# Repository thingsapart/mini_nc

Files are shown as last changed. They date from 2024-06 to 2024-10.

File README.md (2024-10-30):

# MiniNC
The V0 of CNC machines - small envelope with 200x150x70mm (8x6x2.75") work area, aims to cut alu well (enough).

# Discussion
There's a [small discord](https://discord.gg/6VSBqa9H) discussing this machine (and other) small CNCs.

# MiniNC - What is it?
A true small _Desktop CNC_ machine that can be used inside an apartment in a pinch but can still cut softer metals. One that does not require a full shop due to space, mess and noise and does not break the bank. [Current BOM cost is around $500](https://github.com/thingsapart/mini_nc/blob/main/docs/MiniNC%20BOM%20-%20BOM.tsv) with most parts ordered on Amazon, excluding the price to cut the plywood panels (that can add another $100-200 if not diy'd). We're still working on the noise part currently.

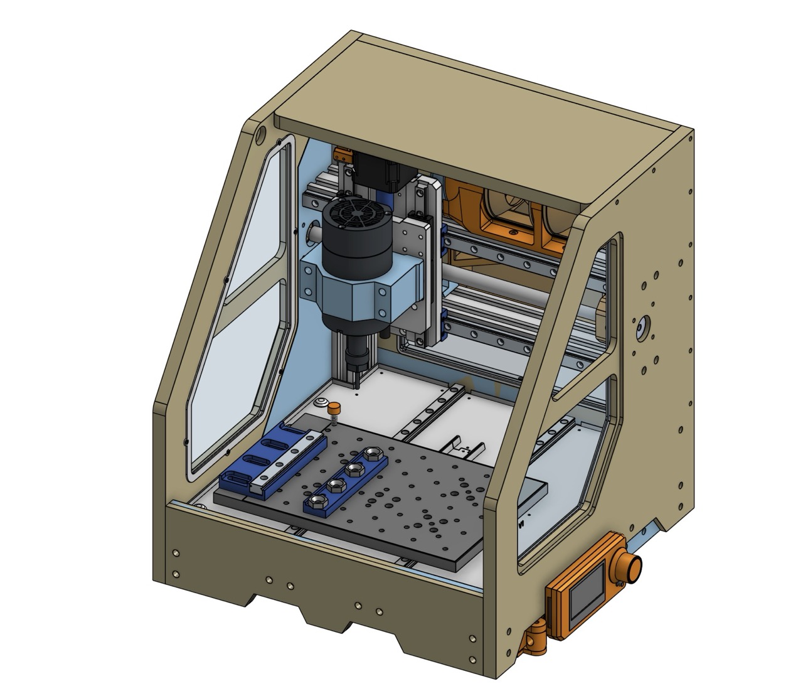
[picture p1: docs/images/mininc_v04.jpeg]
Current status with 300W BLDC spindle, vise, chipvac V2, 3d-touch-probe support, ...


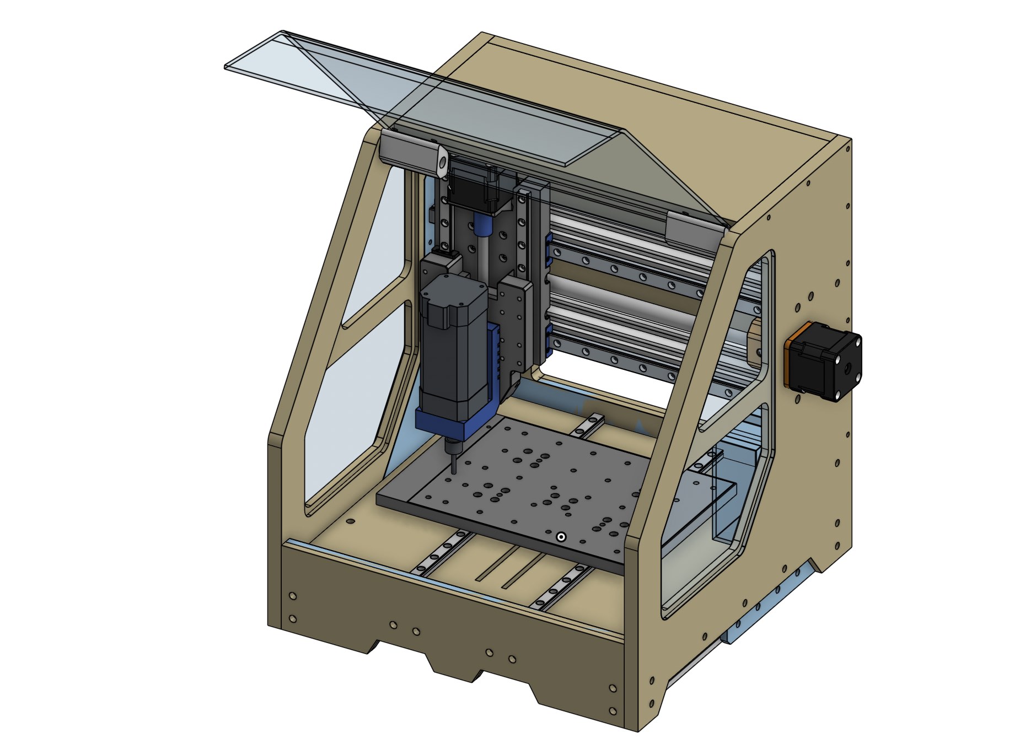
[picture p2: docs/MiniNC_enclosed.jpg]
MiniNC enclosed


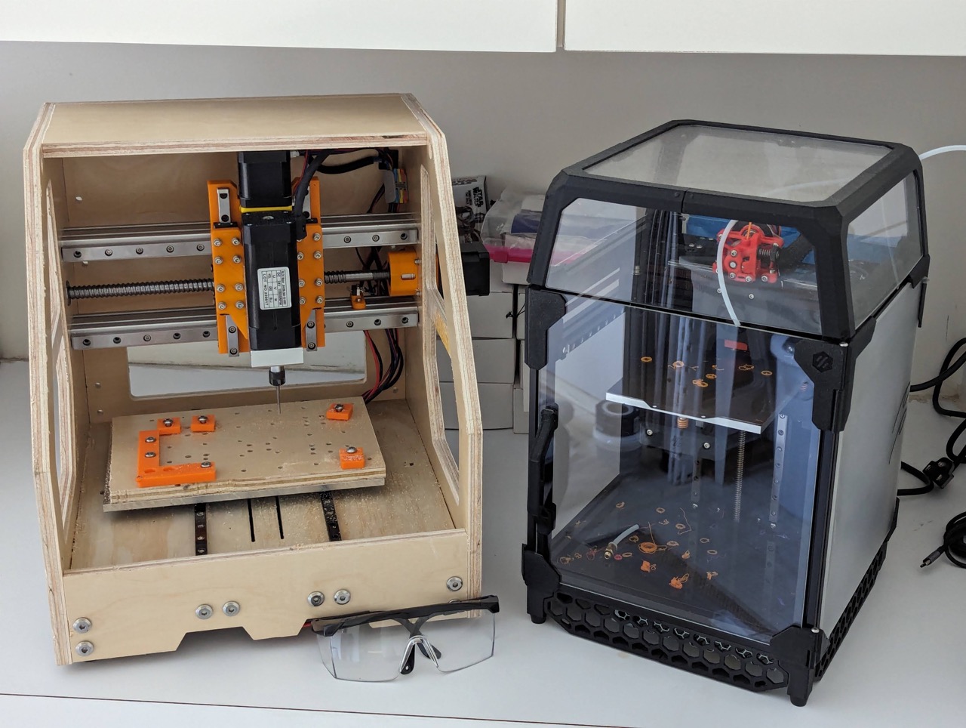
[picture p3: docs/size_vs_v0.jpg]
Size compare to Voron V0.1


## ⚠️ WARNINGS ⚠️
### Danger
CNC machines are a lot more dangerous than 3D printers. BUILD AT YOUR OWN RISK. DO NOT OPERATE "OPEN" OR WITHOUT POLYCARBONATE WINDOWS. TURN OFF THE MACHINE WHEN CHANGING END MILLS OR CHANGING WORK PIECES - DO NOT LEAVE IT POWERED ON WHILE HANDS ARE INSIDE THE ENCLOSURE.
### Alpha
The machine is past the main design phase and a prototype has been built and is about to get tested. But that does not mean everything is finalized.

## Some Results

35x15mm test cut on the first prototype machine (untrammed, excuse the bottom finish) - with 3D-printed ABS X- and Z-plates:
<table style="border: 1px white; border-collapse: collapse;">
  <tr>
    <td rowspan=2>
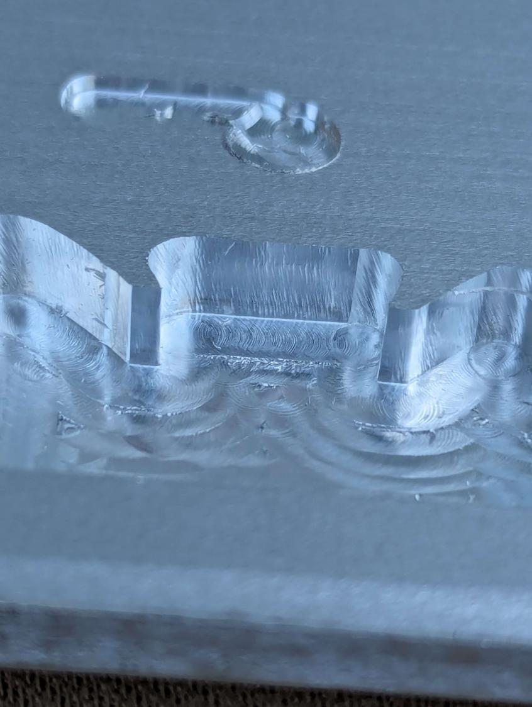
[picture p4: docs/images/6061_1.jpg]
      
    </td>
    <td>
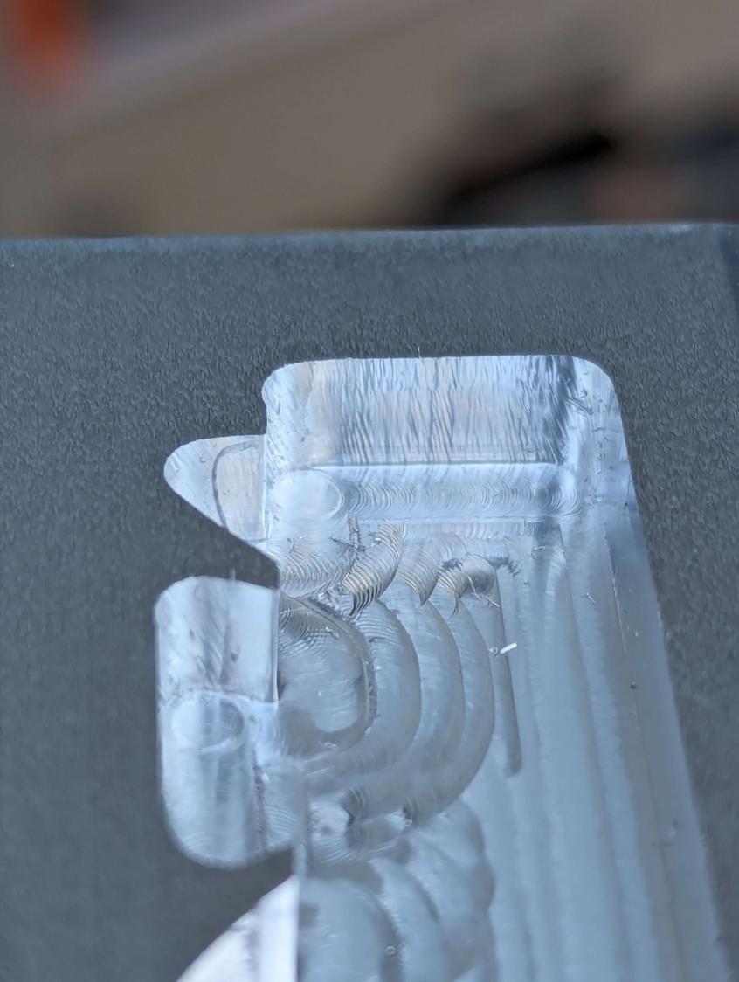
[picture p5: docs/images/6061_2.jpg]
      
    </td>
  </tr>
  <tr>
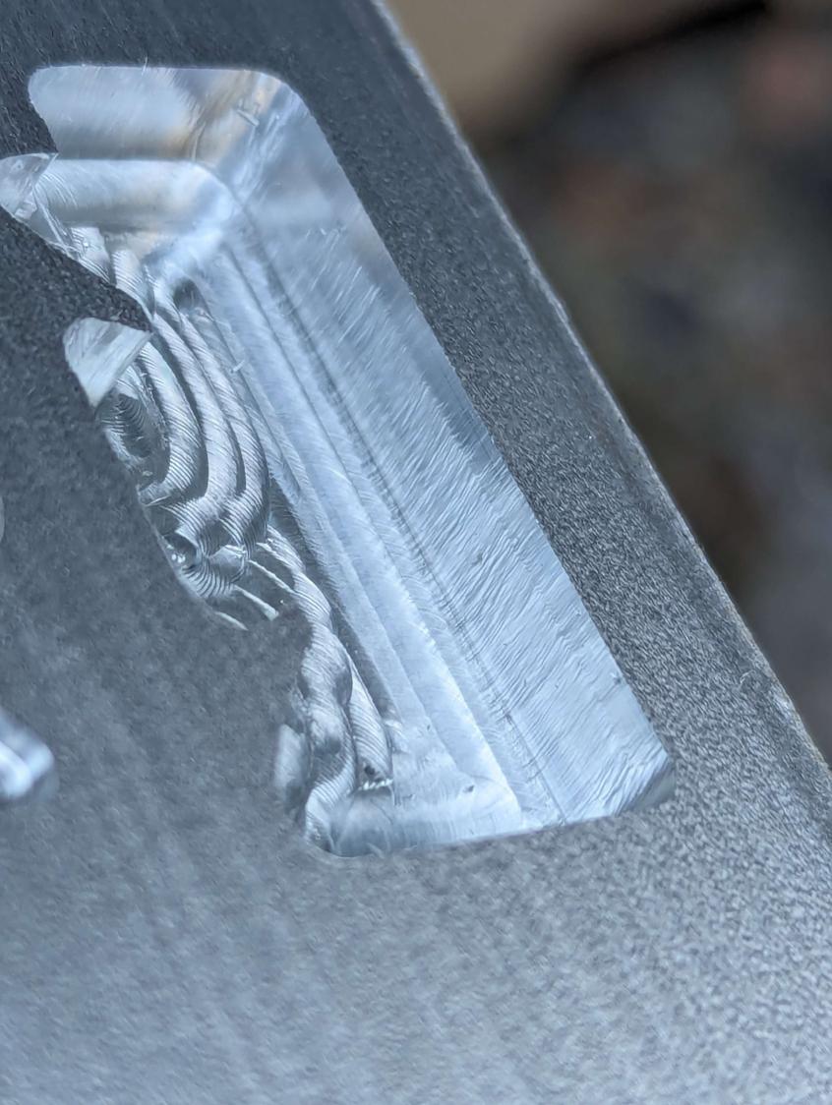
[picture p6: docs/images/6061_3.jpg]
    <td></td>
  </tr>
</table>

## Requirements
* Cuts aluminium well.
* Cost-efficient.
* Space-efficient.
* As quiet as possible.
* Not too messy.

## Inspiration/Credits
This design was influenced by the [Milk Cr8](https://www.milkcr8cnc.com) ([GH](https://github.com/Makers-On-Tap/milkcr8-cnc)) CNC's use of plywood as a stiff box structure to enclose and stiffen the machine at the same time. The idea was to use the wooden structure and combine it with aluminium extrusions to simplify the build while retaining some of the improved dampening over just an alu extrusion structure.

## Features
* Cuts aluminium well =>
   * Rigid (enough) => smaller size, slower feeds, single flute, smaller end mills,
   * As it won’t be the stiffest machine, make it well-dampened => not fully made of alu, use steel, epoxy granite and wood to dampen some of the vibrations,
   * Smaller, low-powered spindles 100-500W,
   * chip-evacuation system => CPAP or chip fan,
   * cooling via misting and air blast.
* Cost-efficient =>
   * Standard components => MGN12/MGN9 rails, small 100-500W spindles, 20 series extrusions for some of the structure,
   * smaller, lower-cost spindles,
   * smaller size.
* Space-efficient =>
   * gantry design => high space-efficiency, can be reasonably rigid in this smaller envelope
   * Smaller size to cut smaller parts fitting target use-cases,
* Beginner-Friendly =>
   * XYZ probe + tool setter + surface meshing,
   * community presets and forums,
   * custom interface for Duet RRF (much later),
      * source  + G-Code + Instructions packages like Coast Runner
      * Integrated forums,
      * g-code visualizer and simulated pre-runner including stock dimensions.
* As quiet as possible =>
   * fully enclosed and ideally tightly sealed,
   * interior/exterior sound insulation (?) => layer of foam + outer layer of ACM panels?,
   * no compressor,
   * BLDC spindles with reduced vibrations.
* Not too messy =>
   * fully enclosed (!),
   * dust extraction => CPAP or roborock fan,
   * misting but no flood cooling.

## Who is it for?
* Makers and 3D printer enthusiasts but really anyone without a full (metal-working) shop and/or space for a larger machine.
* Anyone without the space for one of the larger machines.

## Stiffness

The current wooden frame seems decently stiff at roughly 1N/&micro;m in Y at the spindle collet even with 3D printed X/Y plates - needs more testing though but seems like a good start.

Some general numbers I've found for comparison:
* [Siecni 12x30 Longmill MK2 ~ 0.07N/&micro;m X and 0.05N/&micro;m Y](https://sienci.com/wp-content/uploads/2022/09/Stiffness-Rating-with-Commentary.pdf),
* [MPCNC ~ 0.1-0.2N/&micro;m](https://forum.v1e.com/t/deflection-measurement/37968/34),
* [burly but _large_ CNC build ~ 1-3N/&micro;m](https://www.mycncuk.com/threads/7155-stiffness-measurements-cnc-mk3),
* I've seen 20N/&micro;m recommended for cutting alu very well,
* Milling Machines supposedly ~ 20-30N/&micro;m,
* professional cast-iron or epoxy granite VMCs are on the other 70-150N/&micro;m.
* (LET ME KNOW IF YOU HAVE OTHER/MORE DATA OR CORRECTIONS, I'D LOVE TO ADD IT)
  
NB: [Load cell tool design to apply a measured/specific force to the spindle](https://www.printables.com/model/473947-xy-forcing-mechanism-for-cnc-router-diagnostics).
NB: [Some numbers and suggested values for stiffness](https://www.cnczone.com/forums/uncategorised-metalworking-machines/378098-cnc-2.html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) - 25kgf ~> <0.1mm deflection seems like a decent goal (2.5N/&micro;m).

Rough design for phase-2 buildout using a lasercut steel structure to increase stiffness if needed. 
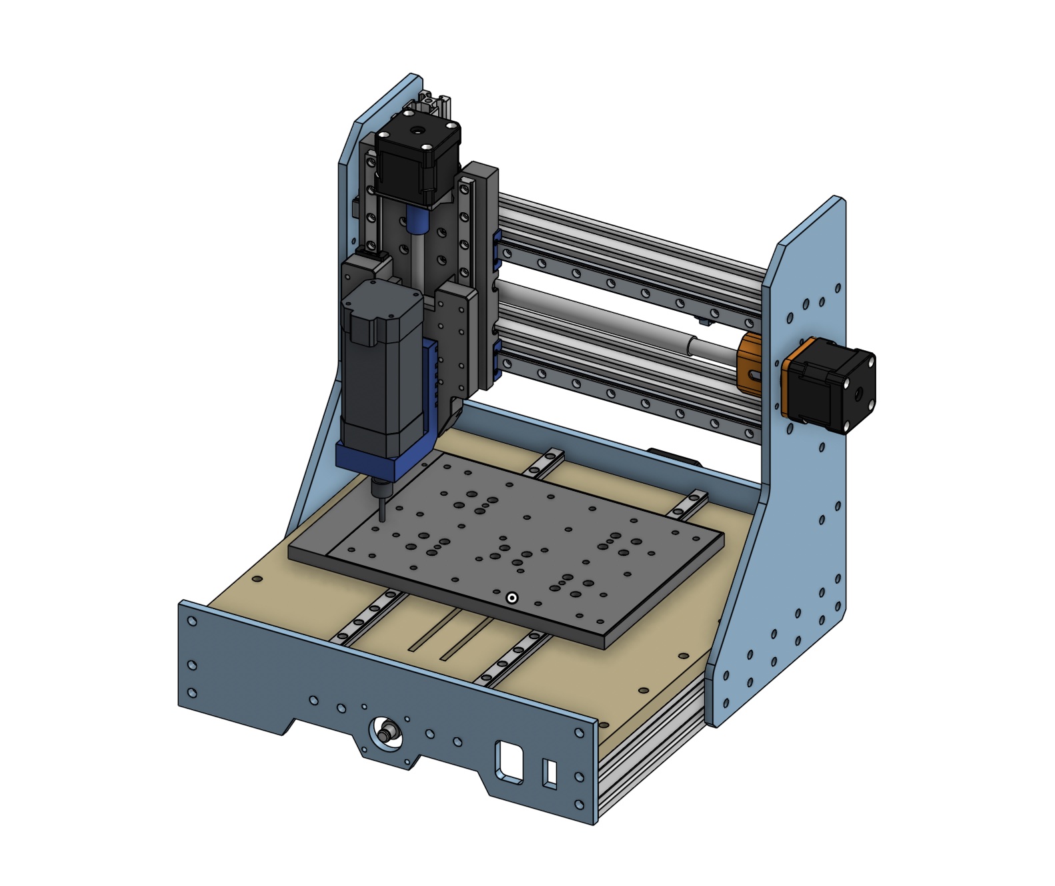
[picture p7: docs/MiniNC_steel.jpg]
Steel structure under enclosure panels


## Chip Vac / Dust Extraction

Finished a small prototype chip-vacuum based on a Roborock/Xiaomi/MiJia vacuum fan and [Roborock-CPAP PCB](https://github.com/condottab/Roborock-CPAP). Additional cost is only ~$15 for the 2kPa fan versions or ~$30 for the (untested) 4-5kPa version.

V2 of the chip vac in a tubular form has been designed and tested, seems to work a tad better than V1 and less prone to clogging, easier to clean.

Supports different "duct attachments" held in place via magnets, which makes it easy to
* remove when changing end mills or cleaning parts of the machine,
* changing the type of attachment (there's currently an open and a closed version with a "curtain", one for better suction, one for better visibility).

Current V2:

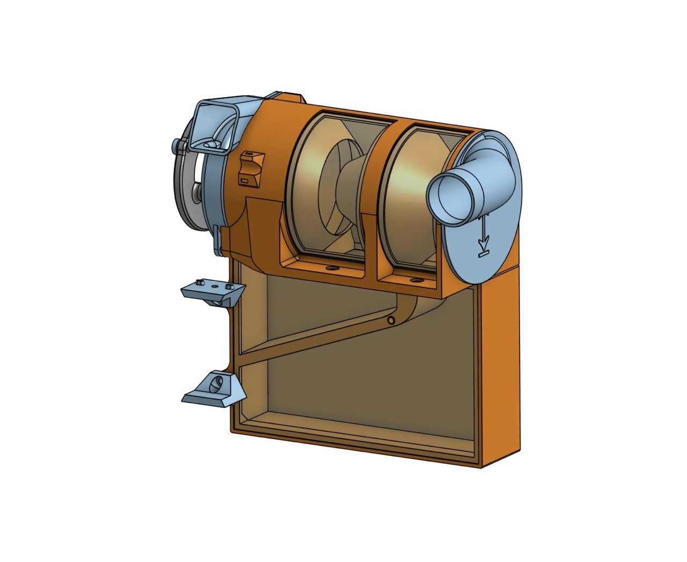
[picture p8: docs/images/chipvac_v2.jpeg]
Chipvac V2


Original V1:

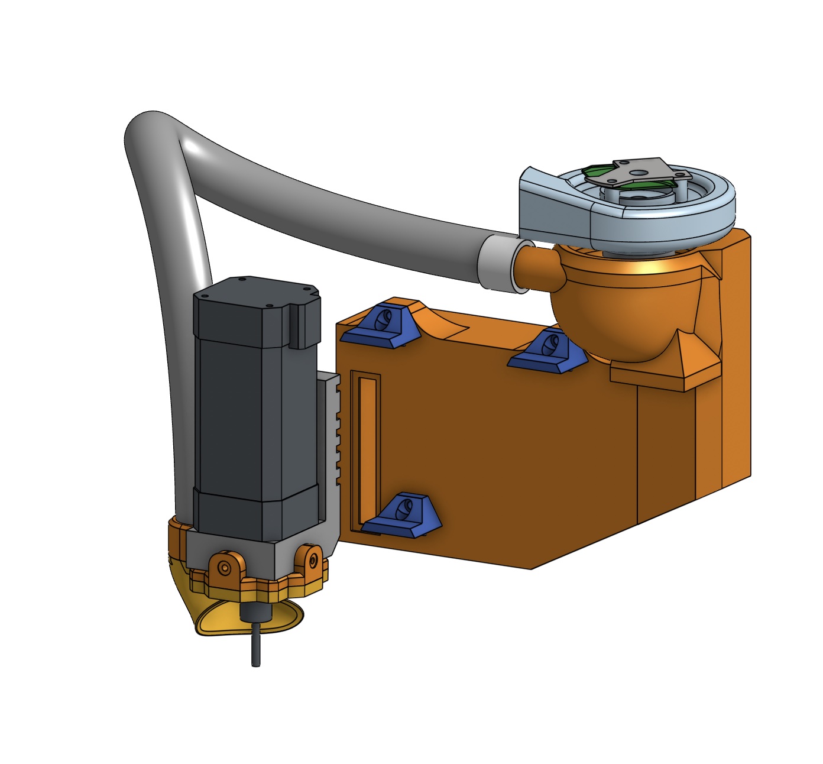
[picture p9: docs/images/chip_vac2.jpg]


## Use-Cases
* Small aluminium parts:
   * high-speed 3D printer motion system reinforcements and brackets,
   * higher-temp 3D printer component,
   * toolhead components.
* Makers:
   * Tools, …

## Optional Features/TODOs
* 🏗 low-profile modular vise system (untested design in V0.2),
* internal camera,
* laser Module Support,
* 🏗 internal LED lighting + toolhead lighting (basic design with room for improvement in V0.2),
* 4th axis?

## Releases
* V0.1 - Initial Release.
* V0.2 - 07/2024
  * Many, many minor improvements after alpha-testing prototype,
  * roboroc-based chip-vac,
  * interla left/right side LEDs,
  * electronics mounts,
  * support for 300W BLDC spindle (36-48V),
  * prototype of MGN9-jaw-based low profile vise,
  * prototype toolsetter (through-bed with fixed switch mounted to bottom panel.
 
[Onshape Document](https://cad.onshape.com/documents/c86121a300cc3efe8d19b16b/w/b3c26184b681d889100ca699/e/cecf7ca72a42132848999341)

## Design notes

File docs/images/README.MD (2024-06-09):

Image files of the machine and samples made with it.

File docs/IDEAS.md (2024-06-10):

# Some (crazy) ideas

## CPAP/Roborock Push-Pull dust extraction and chip blower

Cyclone dust/chip extractor based on a CPAP or Robrock vacuum/blower. Hook up the input port for extraction, the output port for chip blowing and/or misting.

Half of the dust shoe is detachable and held via magnets, the alterantive would be to have two "dust shoe attachments" - one for blowing config, the other for vacuuming.

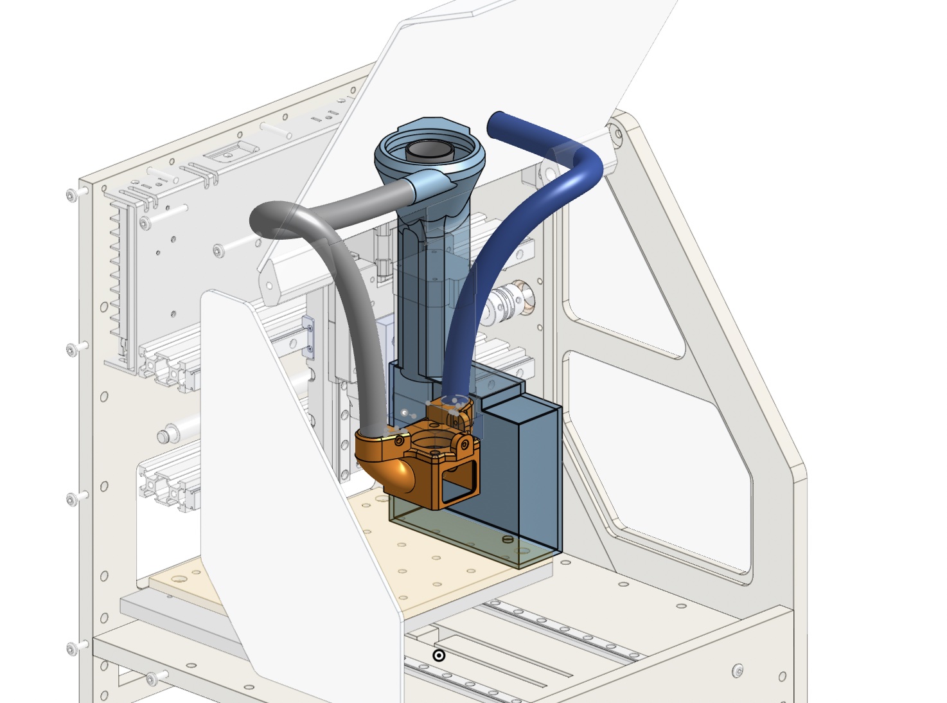
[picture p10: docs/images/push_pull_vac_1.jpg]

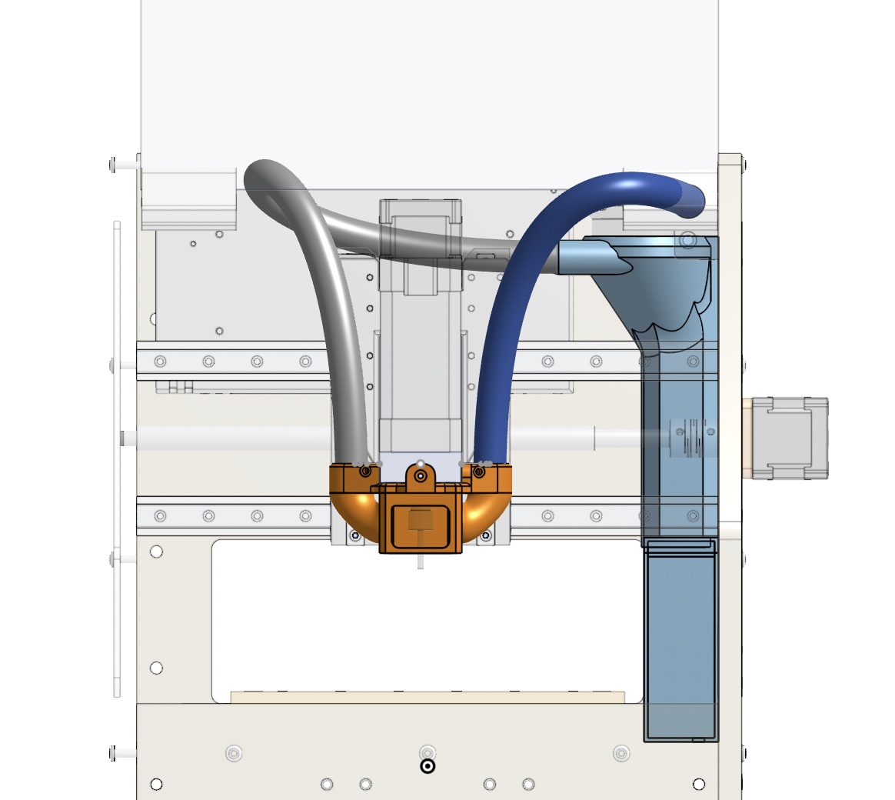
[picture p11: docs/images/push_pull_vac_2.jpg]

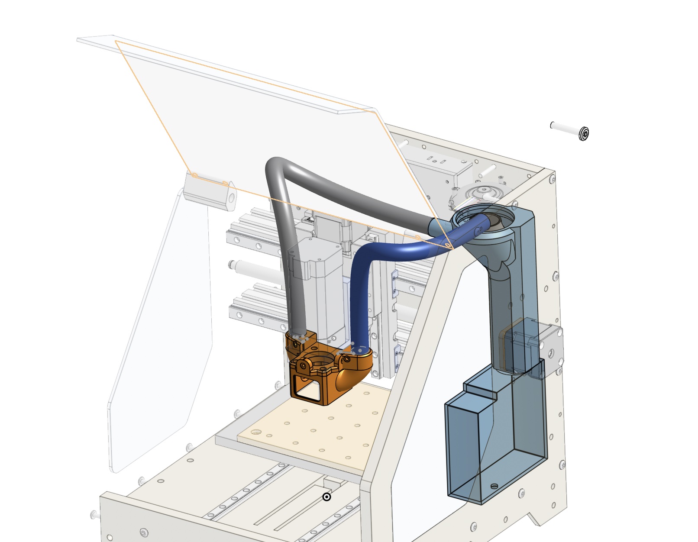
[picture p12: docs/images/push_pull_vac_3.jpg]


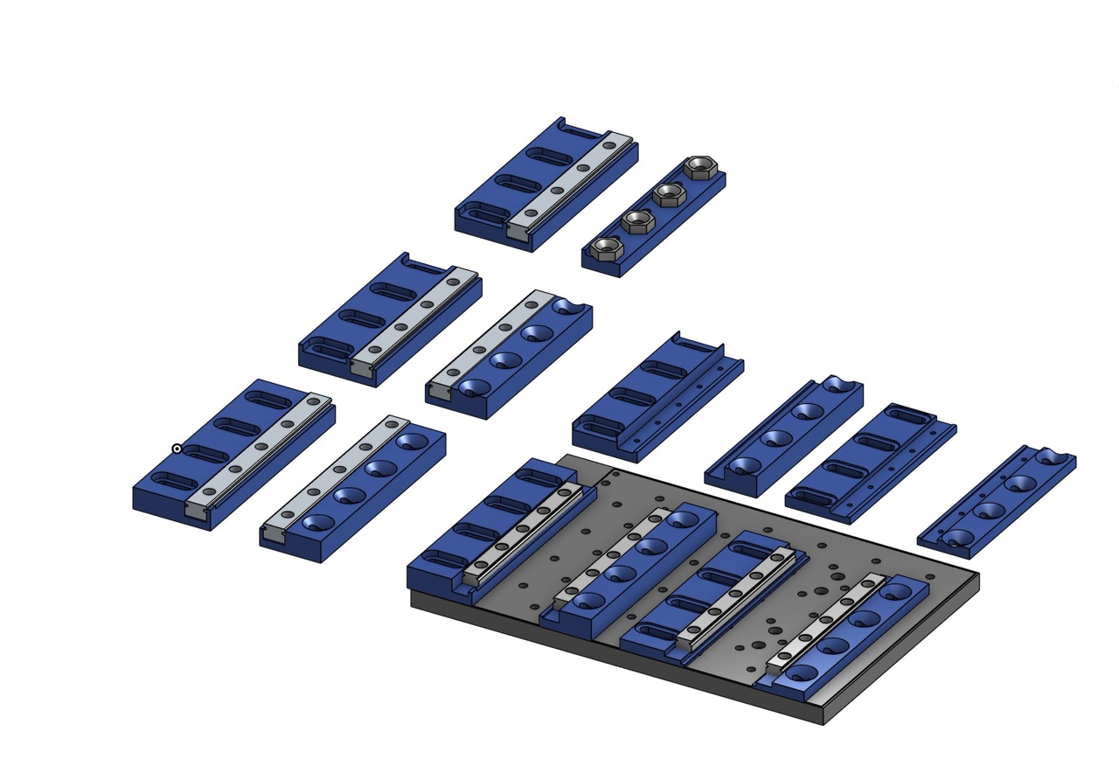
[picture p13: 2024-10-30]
docs/images/vises_v2.jpeg

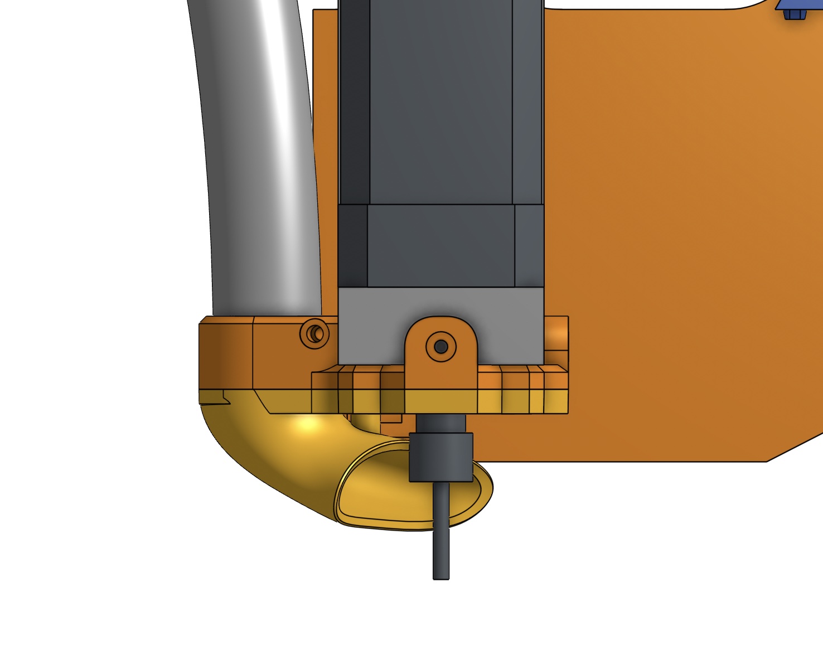
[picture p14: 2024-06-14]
docs/images/chip_vac_open.jpg

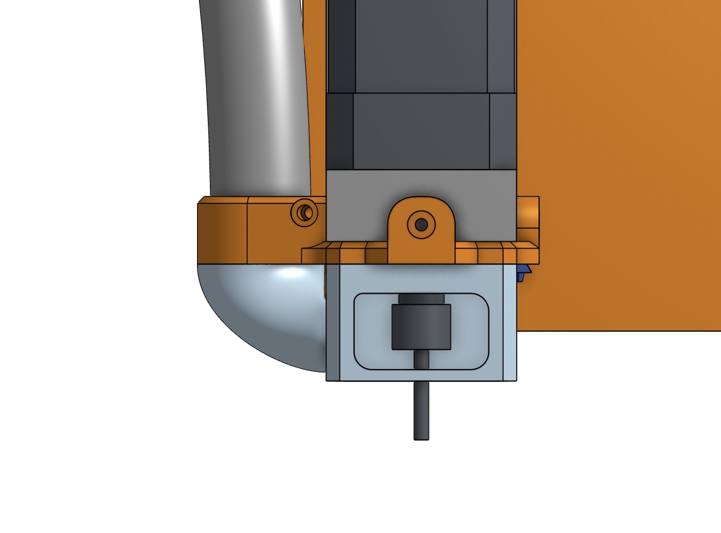
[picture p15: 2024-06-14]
docs/images/chip_vac_closed.jpg

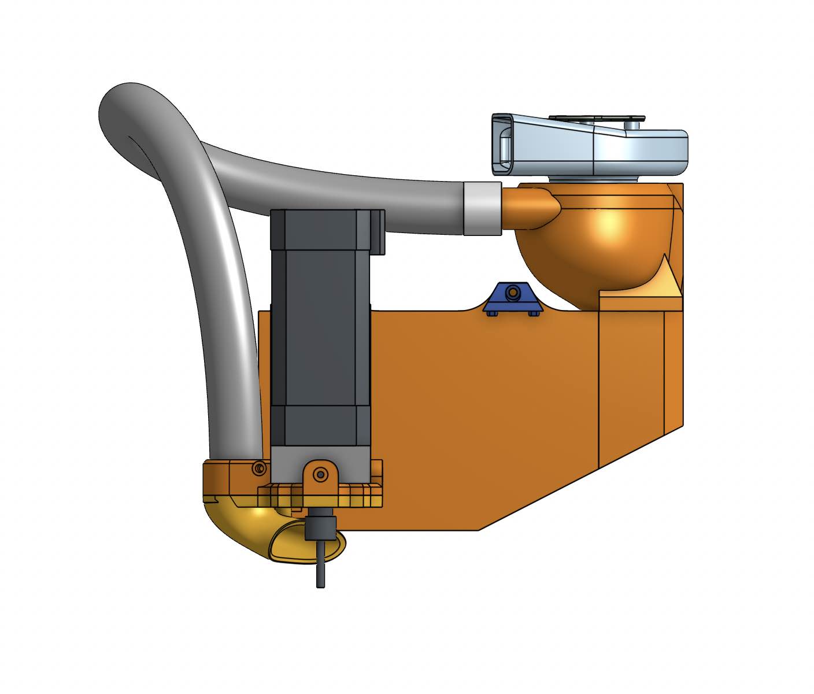
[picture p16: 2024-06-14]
docs/images/chip_vac.jpg

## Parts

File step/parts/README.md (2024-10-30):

STEP and STL files of smaller parts of the machine that might be useful individually.

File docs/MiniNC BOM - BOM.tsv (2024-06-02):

Mechanical |  |  |  | 121.04 | 474.53 | 464.53 | 167.53
 | Rails | 126
 |  | MGN12H 300mm | 4 |  | 50 | 50 |  |  | https://www.ebay.com/itm/325924971185
 |  | MGN12H Carriages | 4 |  | 50 | 50 |  |  | https://www.ebay.com/itm/324798764209 |  |  | https://www.ebay.com/itm/324798763415
 |  | MGN9H 150mm + 4 Carr | 2 |  | 26 | 26 |  |  | https://www.ebay.com/itm/324829197488
 | Lead Screws | 22.5
 |  | 200mm TR8x2 | 2 | 15 |  |  |  |  | https://www.amazon.com/XIAOSHI-Printer-Trapezoidal-Coupling-Bearing/dp/B0B2ZP5FD1
 |  | 100mm TR8x2 | 1 | 7.5 |  |  |  |  | https://www.amazon.com/ReliaBot-100mm-Thread-Printer-Machine/dp/B092YV88MB
 |  | SFU1204 Ballscrew 300mm | 2 | 40 | 40 | 40 |  |  | https://www.amazon.com/gp/product/B0CP21P5HP
 |  | 100mm T8 + rigid coupler | 1 | 8 | 10 | 5
 | Nuts | 10
 |  | OpenBuilds anti-backlash nut | 1 |  | 10 | 5 | 10 |  | https://www.amazon.com/GLEAVI-Accessories-Anti-Backlash-Ballcock-Printers/dp/B0CSBCDJLN
 | Extrusions | 20
 |  | 2040 300mm | 4 |  | 20 | 20 | 20 |  | https://www.amazon.com/BELLA-BAYS-Extrusion-20mmx40mm-Engraving/dp/B0B7HLWZNH
 |  | 2040 250mm | 2 |  | 8.99 | 8.99 | 8.99 |  | https://www.amazon.com/BELLA-BAYS-Extrusion-Engraving-Workbench/dp/B0BM8HSLX7/
 |  | 25x25x2mm Alu Square Tube | 1 |  | 12 | 12 |  |  | https://www.amazon.com/dp/B07ZVNN28B
 | Couplers | 8.54
 |  | 8mm to 5mm Couplers | 2 | 8.54 | 8.54 | 8.54 | 8.54 |  | https://www.amazon.com/Zeberoxyz-Coupling-Aluminum-Diameter-Connector/dp/B08ZJ854Z6/
Electronics |  |  |  |  |  |  |  |  | https://www.amazon.com/Aluminium-Flexible-Coupling-Diameter-Connector/dp/B08JZ1D5BY
 | Control | 55
 |  | FLY E3 Pro V3 / SKR2 / FLY CDY V3 / RRF something | 1 |  | 30 | 30 |  |  | https://www.aliexpress.us/item/3256802186437082.html
 |  | PSU MW LRS-350-24 | 1 |  | 25 | 25 |  |  |  | Back-Mounted
 |  | PSU MW UHP-350-24 | 1 |  |  |  |  | 75 |  | Under-Mounted
 |  | Alt: NDR-480-48 + 24V-stepdown | 1 |  |  |  |  | 49 | https://www.ebay.com/itm/176235897041
 |  | Alt: 2x cheap 150W+ LED PSU |  |  |  |  |  | 20 | Aliexpress
 | Motors | 87
 |  | OMC 48mm | 1 | 42 |  |  |  |  | https://www.amazon.com/STEPPERONLINE-Stepper-Bipolar-Connector-compatible/dp/B00PNEQKC0
 |  | T8 Lead Screw Stepper 200mm/240mm | 2 |  |  |  | 58 | 58 | https://www.amazon.com/Iverntech-NEMA-17-Stepper-Motor/dp/B07LF2GGJ4?th=1 |  | https://www.amazon.com/FYSETC-Replacement-leadscrew-9-44inch-Compatible/dp/B0B63FGNJX/
 |  | T8 Lead Screw Stepper 150mm | 1 |  |  |  | 29 | 29 | https://www.amazon.com/Iverntech-NEMA-17-Stepper-Motor/dp/B07LF2GGJ4?th=1
 |  | Nema17 48mm Steppers (ideally 2A) | 2 |  | 33 | 33 |  |  | https://www.amazon.com/Stepper-Motor-59Ncm-4-wire-Printer/dp/B00Y2HJE22/
 |  | Nema17 39/40mm Stepper (ideally 2A) | 1 |  | 0 | 0 |  |  | https://www.amazon.com/Stepper-Motor-Bipolar-64oz-Printer/dp/B00PNEQI7W/
 | Spindle | 50 |  |  |  |  |  | 68
 |  | Alt: 300W Brushless (with mount?) | 1 |  |  |  |  | 90 | https://www.aliexpress.us/item/3256804988257371.html
Filament |  | Genmitsu 60W Spindle + NDR-120-24 + DualFOC ESP32 ~> 150W |  |  |  |  |  | 50 | https://www.aliexpress.us/item/1005005935486903.html | https://www.ebay.com/itm/375131593389
 |  | 104W BLDC Spindle + controller | 1 |  | 73 | 73 |  |  | https://www.amazon.com/dp/B08CMHPJ3S
Fasteners + Bearings
 |  | Various M3 + T-Nut + Drop-in T-Nuts | 1
 |  | Various M5
 |  | M6x1 30mm Flat Head Hex | 45 |  | 10 | 10 |  |  | https://www.amazon.com/gp/product/B0CK2H57YV/
 |  | M6 Cross Dowel / Barrel Nuts | 38 |  | 10 | 10 |  |  | https://www.amazon.com/gp/product/B07CKYH8WR/
Plywood |  | 1/2 in Baltic Birch 30inx30in | 1 |  | 33 | 33 | 33
Acrylic
Bed
 |  | 8x12in 1/4in 6061 plate | 1 |  |  |  |  | 18
 |  | 8x6in 3/8in Cast Tooling Plate | 1 |  | 25 | 25

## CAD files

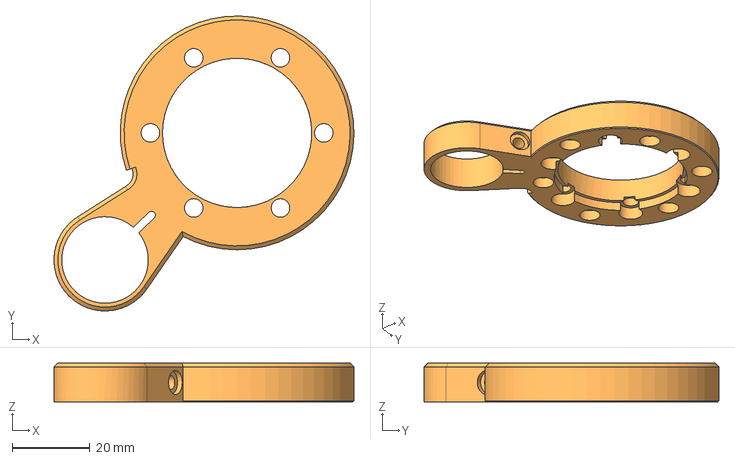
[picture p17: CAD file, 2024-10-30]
step/parts/300W Spindle Dust Shoe - 300W Spindle Dust Shoe Base.step
77.0 x 75.7 x 10.0 mm

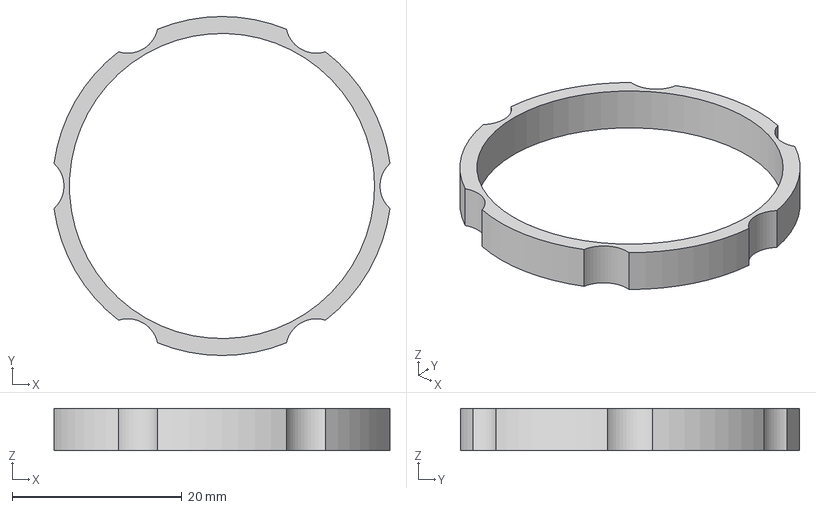
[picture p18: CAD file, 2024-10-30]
step/parts/300W Spindle Dust Shoe - 300W Spindle Dust Shoe Mid Gasket.step
39.6 x 40.0 x 5.00 mm

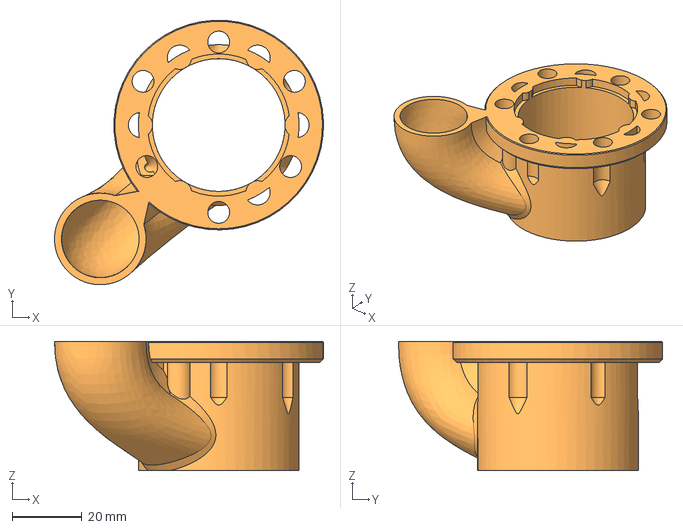
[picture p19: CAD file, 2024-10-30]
step/parts/300W Spindle Dust Shoe - 300W Spindle Dust Shoe Ext.step
77.0 x 75.6 x 37.0 mm

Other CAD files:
step/prev/MiniNC Steel-Alu.step
step/parts/300W Spindle Dust Shoe - 300W Spindle Dust Shoe Base.stl
step/parts/300W Spindle Dust Shoe - 300W Spindle Dust Shoe Mid Gasket.stl

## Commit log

2024-06-02 Prelim BOM TSV
    [MiniNC BOM - BOM.tsv]
2024-06-02 Attempt to quote TSV with CSV rules for GH preview
    [MiniNC BOM - BOM.tsv]
2024-06-02 Another attempt at quoting
    [MiniNC BOM - BOM.tsv]
2024-06-02 Update MiniNC BOM - BOM.tsv
    [MiniNC BOM - BOM.tsv]
2024-06-09 Samples images
2024-07-18 Rename step/MiniNC Steel-Alu.step to step/prev/MiniNC Steel-Alu.step
    [MiniNC Steel-Alu.step]
2024-10-30 Dust shoe for the 300W spindle
    [300W Spindle Dust Shoe - 300W Spindle Dust Shoe Base.step, 300W Spindle Dust Shoe - 300W Spindle Dust Shoe Ext.step, 300W Spindle Dust Shoe - 300W Spindle Dust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]
2024-10-30 300W Spindle Dust Shoe STL files
    [300W Spindle Dust Shoe - 300W Spindle Dust Shoe Base.stl, 300W Spindle Dust Shoe - 300W Spindle Dust Shoe Mid Gasket.stl]
